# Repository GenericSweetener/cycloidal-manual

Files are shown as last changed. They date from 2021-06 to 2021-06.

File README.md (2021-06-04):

# Sections
## 1 – [Intro](https://github.com/GenericSweetener/cycloidal-manual/blob/main/README.md#11--introduction)
## 2 – [The Concepts and Components](https://github.com/GenericSweetener/cycloidal-manual/blob/main/README.md#21--the-concepts-and-components)
## 3 – [Snap Back to Reality](https://github.com/GenericSweetener/cycloidal-manual/blob/main/README.md#3--snap-back-to-reality-1)
## 4 – [Design & CAD](https://github.com/GenericSweetener/cycloidal-manual/blob/main/README.md#4--design--cad)
## 5 – [Closing and Sources](https://github.com/GenericSweetener/cycloidal-manual/blob/main/README.md#5--closing)

This guide was created for a senior capstone project at Templeton Academy based on this research question: 

What are the appropriate use cases for, benefits and drawbacks of, and best construction practices for common complex gear sets in terms of 3d printed hobbyist construction for high torque applications?

It does not answer that question (see section 5).

# 1.1 – Introduction
Cycloidal drives/reducers are extremely useful components to have at one’s disposal when working in hobbyist robotics, however a lot of the material aimed at beginners tend to be lacking in substance, missing practical application, or in some way fail to offer a complete guide through creating cycloidal drives from scratch. This is not to say that there aren’t useful materials out there, it’s just that one often has to cobble a number of them together to integrate cycloidal gearing into their project. Thus, this document was created to be a plain English single resource for understanding the theory of operation behind cycloidal drives, and understanding the methods of and best practices for their construction.

## 1.2 – The Target and Scope
Cycloidal drives have a broad range of uses in a number of fields and applications, but with that comes an extremely broad range of appropriate contents for this document. To that end, the scope of this guide has been limited somewhat by the project that sparked it, namely the joints of a low budget quadrupedal robot, called S.N.O.T (Sub-Nominal Operations Testbed) (will be linked here if files are ever published). S.N.O.T uses nema 17 stepper motors for all joints (a poor decision in retrospect) which are capable of outputting ~0.34 N⋅m of torque. The gearboxes created for this project are intended to fit into a modular system created for S.N.O.T that has space for gearboxes 60mm in diameter and ~22mm thick. The chosen target gear ratio for the cycloidal drives is 30:1, which while likely not enough to walk with, is plenty for experimenting on the test stand. The reducers are also required to be as cost reduced as possible to fit within the budget, and will be primarily 3D printed.

TLDR; We’re using nema 17 stepper motors to power 3D printed cycloidal drives of a similar footprint in robotic leg joints.

## 1.3 – Materials, Tooling, and Software
Unless otherwise stated, all modeling for this project has been done in FreeCAD, sliced for printing in Ultimaker Cura, and printed on an Creality Ender 3 using Overture PLA filament.

While all modeling was done in FreeCAD, this guide is intended to be usable with any parametric modeling software, save for the creation of the cycloidal disk (see section 4.1.1 for more). 

# 2.1 – The Concepts and Components
While this guide gets around having the user complete the majority of the complex math behind the concept of cycloidal gearing, an understanding of the theory of operation and components therein is still vital to utilizing the rest of this guide.

## 2.2 – The Basics

Cycloidal drives offer a relatively high torque density, especially compared to standard involute gearing. The way this is accomplished is visually complex, but simple enough when stripped down to the base concepts. As the name suggests, cycloidal drives rely on the concept of cycloidal, or more specifically, hypocycloidal paths. A cycloidal path is effectively the result of rolling a circle along a straight line, tracking a single point on the diameter of the circle, and plotting the position of that point as the circle rolls as a new line.  

Cycloid_f
> By Zorgit - Own work, CC BY-SA 3.0, https://commons.wikimedia.org/w/index.php?curid=4552689

Hypocycloidal paths are the same as cycloidal paths, except the circle is rolling around another circle instead of on a straight line.



While every element of a cycloidal drive is not a direct product of this concept, they all have something to do with the idea of a circle rolling around within another circle, so just keep that in mind.

## 2.3 – Getting a Grip (base understanding)


> By Petteri Aimonen - Own work, Public Domain, https://commons.wikimedia.org/w/index.php?curid=7732225

If the above animation makes sense to you immediately, good job, you get to skip most of this section. For the rest of us, this is going to take some unpacking. Rather than pick apart the actual components of a cycloidal drive, let’s start with something more conceptual. A cycloidal drive is at its core a circle, called the cycloidal disk, rolling around the inside of another slightly larger circle, called the housing (soon to be drive pins). At face value, this does not appear to be any sort of speed reducer, until one considers how it can be driven.

without shaft
> Apologies for the poor quality. Also, please note that the video loops where you see the tracked point jump.

This is where the bearing and eccentric shaft (green component of the main 3D animation) come into play. To drive the cycloidal disk’s rolling motion, there are a number of ways one could theoretically transfer power to it, but to achieve the effect of a gear reduction, there is a rather clever and simple method. First, a bearing is placed in the center of the cycloidal disk, and then the motor is attached off center to a shaft inside it. 

with shaft
> Yeah, still not sure what the yellow in the gif is. This shows 1 rotation of the input shaft / motor. Note how much the disk actually rotates.

This both means that the power source/motor is isolated in terms of rotational speed from the cycloidal disk, because the inner and outer race of the bearing can spin at different speeds, and, because the motor is off center by the same amount as the difference between the diameters of the cycloidal disk and housing, the disk is always pressed against the edge of housing. The degree to which the motor is off center is called eccentricity, and will play more of a role later. Put this all together, and when running the motor the cycloidal disk will not spin with the motor, but instead will roll along the inside of the housing, and because the circumference of the disk and housing are similar, the disk can be rolled around for one rotation of the motor but only actually spins a small amount. This is in effect a gear reduction because 1 revolution of the motor on the eccentric shaft results in less than one rotation of the cycloidal disk.

However, even if this were taking place in an ideal world where no power was lost to friction, and the cycloidal disk never slipped, there is still no mechanism by which to actually utilize the power being transferred, because the cycloidal disk is not centered and can’t have an output shaft mounted directly to it.

## 2.5 – Getting an Output (output pins and holes)
Getting power out of a cycloidal drive is less about directly connecting the cycloidal disk to an output shaft and more to do with rectifying the wobbling motion of the disk as it rotates so that the gear reduction created can actually be used. This is where the output holes and pins seen in the animation (purple) come into play. The rectifying method of choice here uses at least 3 (normally more) holes in the cycloidal disk spaced equally in a circular pattern on its face, shown below on a reference circle of a known size. 

Screenshot from 2021-06-03 16-17-28

These holes then correspond to output pins/rollers that are arranged in the same fashion and on a reference circle of the same diameter as the reference circle of the holes.



hese pins are mounted to a surface that can rotate, called the output disk (seen in purple in the animation), which is centered by a bearing of some sort in reference to the housing. What makes it possible for these output pins to mesh with the holes of the disk even though the disk is not centered while rotating is that the disk’s holes are the same as the diameter as the output pins plus the eccentricity of the disk. This in effect means that while the output pins are never centered in the output holes, their sides are able to contact the edges of the holes, rolling along the inside of the output holes and being pushed in the correct direction. This is why there need to be more than one set of pins and holes to prevent slop in the output from the pins not being directly attached to the disk, instead requiring multiple angles of contact.

## 2.6 - Getting It To Work (the cycloidal disk and drive pins)
Up until this point, a simplified model of the actual mechanism by which the gear reduction is created has been used to demonstrate the concepts around it, however this model would be extremely inefficient and borderline useless in any practical application. So, instead of relying on the friction between a smooth cycloidal disk and its housing, cycloidal drives use a set of drive  pins/rollers in the housing (silver), and a disk with corresponding lobes for those pins which is the cycloidal disk (yellow). 



> By Petteri Aimonen - Own work, Public Domain, https://commons.wikimedia.org/w/index.php?curid=7732225

The same movement is happening here as before, that wobbling roll is the same as when it was 2 simple circles, but now there’s multiple points of contact being made so the disk can’t just slip around, it can only rotate on its rolling path. The interaction between the pins and lobes is also a similar motion to the circle rolling around another circle, one could think of the disk as the pattern made by rolling one of the pins around a circle. It is also at this point that the number of pins in the housing compared to the number of lobes on the cycloidal disk come into play. Knowing that the lobes on the disk and the drive pins are in roughly the same scale to each other, similar to gear teeth, if there were the same number of pins and lobes then the disk would not be able to move because it would just be sitting locked into the pins.



That’s just going to bind up.

This is why, in this guide and in most cycloidal reducer designs, there is one more pin on the housing than there are lobes on the disk. Not only does this make room for the rolling motion to be possible in the first place, it defines the transmission ratio of the reducer in more solid terms than the difference between the circumference of 2 circles. This is to say that for every full rotation of the input shaft, the disk moves 1 (or whatever the difference between the number of pins and lobes is) pin over. With this knowledge, the gear ratio can be defined. In this example of 30 pins on the disk and 31 pins in the housing, it would take 30 rotations of the input shaft to make one full rotation of the cycloidal disk, making the transmission ratio 30:1.

## 3 – Snap Back to Reality
An understanding of the theory of operation is only so good as the practical application of those concepts. To that end, this section will translate the concepts from section 2 to what one may actually want to manufacture.

## 3.1 – Variants of the Design

This guide offers 2 main variants of the cycloidal reducer. The first is what is generally considered to be the standard design and is what is described throughout section 2, using a plate connected to the output pins as the power output for the reducer. This design will be called the driven disk design going forwards. The second variant is conceptually the same as the first, but has fixed output pins and instead rotates the housing (called the driven housing design in this guide). 

> [Standard cycloidal reducer full assembly (video)](https://youtu.be/JAcRD82Ofww)

### 3.1.2 – Driven Housing

The best way to conceptualize driven housing designs is to imagine the housing as being free floating and the cycloidal disk as limited in its range of motion to just its wobble. This is accomplished by mounting the output pins to a stationary plate, in this case the one the motor mounts to. This component is referred to here as the motor plate or lower pin plate. Now, when the housing interacts with the disk, the disk can’t rotate but the housing can, so it does.

> [Moving housing cycloidal drive in operation (video)](https://youtu.be/8ANe9f_OlMg)

Of course, the housing needs to be kept centered, won’t survive much torsion if only supported on one side, and the forces applied to it shouldn’t be transferred to the cycloidal disk. For those reasons it’s stabilized by a bearing on the top and bottom. The bottom bearing connects to the motor plate, and the top bearing connects to a plate that has screws running down through the drive pins to connect to the motor plate.

> [Drivin Housing cycloidal reducer full assembly (video)](https://youtu.be/nldJB2Xw-ws)

### 3.1.3 – A Note on Stacked Disks

While not utilized in this guide, it is common practice to reduce the vibration caused by the off center rotation of the cycloidal disk by having 2 disks in the same housing 180 degrees offset from each other. 

Screenshot from 2021-06-03 16-28-52

These disks will rotate in the same direction and at the same speed so their output holes still line up with each other (provided they are symmetrical across both the x and y axis). This means that while rotation is still taking place, the shifting weight of one disk is always offset by the other. To accomplish this the eccentric shaft is split into 2 cams so the top and bottom disks are driven 180 degrees offset from each other.

Screenshot from 2021-06-04 09-00-27

## 3.2 – Bearings – An Epic Saga
Anyone genuinely considering manufacturing a cycloidal drive by means of 3D printing will have likely noticed the very high number of surfaces that need to be in contact with each other in even the most basic of cycloidal designs. The good news is that all but the edge face of the cycloidal disk can be replaced by a friction reducing element, however this may not always be the best design decision. At any rate, a cycloidal drive that will carry any sort of load requires at the very least 2 bearings: 1 in the center of the cycloidal disk and another to keep the output ring centered. 

### 3.2.1 – The Required Bearings – Cycloidal Disk
The bearing in the center of the cycloidal disk (drive bearing) both relies on and can limit some of the primary dimensions of the cycloidal drive, so care should be taken when finding a bearing to use. Firstly, keep in mind that this bearing is what makes it possible to use an eccentric shaft, so some thought needs to be given to the inner dimension of the bearing so that the the desired level of eccentricity is both possible and won’t create a situation where the hole in the eccentric shaft that accepts the input shaft of the motor is extremely thin on one side. (learned that the hard way).

Screenshot from 2021-06-04 09-03-49

A good rule of thumb is that (assuming the eccentric shaft is accepting a metal output D-shaft from the motor) the inner diameter of the bearing should be equal to the diameter of the motor output shaft plus the disk’s eccentricity plus however thick you want the thinnest part of the eccentric shaft to be (at least 3mm).

Another point to consider is that the cycloidal disk should be a similar thickness to the drive bearing. This ensures that the bearing will be able to transfer power to the entire edge of the cycloidal disk. It’s also a good idea to have a ridge of some sort modeled in the hole for the bearing so it can be pressure fit until bottoming out.

Screenshot from 2021-06-04 09-05-26

One final element of note is that, especially with a 3D printed disk, the bearing is likely to be the heaviest spinning component, and will be spinning off center to the rest of the assembly. This can be dealt with by using a stacked design (see 3.1.1), but suffice it to say that a lighter bearing will create less vibration.

### 3.2.2 – The Required Bearings – Output Pins / Output Ring (output bearings)
To center the output disk/pins to the housing, it is advised that a relatively large bearing is used with an inner diameter that is able to fit around the outside of the output disk, and is therefore larger than the outer edge of the output pins. This then mounts into the housing.



This method allows the forces applied to the output ring to be braced against the housing, which can be reinforced depending on the load required. While this method is strong and robust, it does have some drawbacks. Cost is by far the largest issue bearings of this specification can add to a project, with the example bearings (inner diameter = 45mm, outer diameter = 85mm, thickness = 7mm) costing roughly $10 per bearing, which can get quite expensive for something like a quadrupedal robot, especially when using cycloidal designs that require 2 output bearings (3.1.2). These larger bearings are also quite heavy, the aforementioned bearings in particular weigh ~50g.

### 3.2.3 – Output Pins

Using something other than 3D printed plastic for output pins is by far the most valuable upgrade one can make to their budget cycloidal drive, because it increases the strength of the assembly by a massive degree without adding too many more individual components. The drawbacks of 3D printed output pins is quite obvious when one considers the relatively low force required to shear off the pins on the layer lines. 

Screenshot from 2021-06-04 09-15-10

> Video of pin failure [here.](https://youtu.be/O2v3M0Q1Ow4)

The 2 routes one can take in making reinforced output pins are using small bearings or using round nylon standoff spacers in place of 3D printed output pins. The only real difference from a modeling and construction perspective is that rather than modeling pins to be printed on the output disk, one would have holes through it, potentially with hexagonal holes on the other side going partially through it to capture a nut. And of course a bolt/screw and a nut is necessary to keep the bearing / nylon spacer in place (as seen in 3.2.2).

This guide uses 7mm outer diameter 3mm inner diameter nylon spacers as output pins.

### 3.2.4 - Drive Pins
Using bearings in place of 3D printed drive pins can significantly reduce wear and friction within a cycloidal drive, however these benefits come with increased weight, drive pin diameter, cost, and complexity. To that end this guide did not include testing with bearings in place of drive pins and does not have modeling instructions for them. 

### 3.2.5 – A Note on Pressure Fitting Bearings
This guide requires a fair number of bearings to be pressure fit into 3D printed housings, so some thought and testing of bearing fitment should be done before printing components. It is therefore advised that you create test pieces for bearings to fit into / to fit into bearings and undergo some trial and error to find dimensions that can tightly hold or fit into a bearing without being deformed by it or requiring forceful persuasion (Take it from someone who’s broken a bearing with a hammer). When making test pieces, be sure to use the same print settings as on the final components. Time spent in this process will save on test prints later down the line.

## 3.3 – Choosing an Output Pin Circle
The output pin circle is the reference circle that passes through the center of the output holes on the cycloidal disk and through the center of the drive pins as mentioned in section 2.5. Especially on the smaller cycloidal disks used in this guide, it is of the upmost importance to ensure that the output holes on the cycloidal disk have enough material surrounding them as to not create thin weak spots in the disk for deformation or cracking to occur. A good rule of thumb is to have the output pin circle roughly centered on the disk, and try to have ~3mm of material around the holes.

Screenshot from 2021-06-04 09-17-33

However, this is not always possible because the inner diameter of the drive bearing can limit the maximum size of the output pin circle, and should also be taken into account. This is why the output holes on the reference models provided are not perfectly centered on the cycloidal disk.



# 4 – Design & CAD
Now for the long boring part. This section is a step-by-step guide for designing the various components of driven housing and driven disk cycloidal reducers. The reference models created for this project are provided here in .FCStd format, editable and exportable in FreeCAD.

## 4.1 – Cycloidal Disk
This guide uses the process of modeling the cycloidal disk as the focal point for setting all major parameters of the cycloidal drive.

### 4.1.1 – Why FreeCAD?
The two common ways to model a cycloidal disk are mathematically defining it from scratch as a curve, or using a disk generation tool that creates a disk based on easily inputted parameters. This guide is aimed at beginners to cycloidal gearing, and so it was decided that a disk generation tool should be used to lower the overall difficulty for the end user. Because FreeCAD was used for all modeling in this project, the [FCGear workbench](https://wiki.freecadweb.org/FCGear_Workbench) was used to generate the disk. However, because this guide is intended to be usable agnostic of the chosen modeling software, this section has been split into a video which walks a user through the complete process, from installing FreeCAD to exporting the disk for printing; and a written section intended for those already familiar with FreeCAD.

If, however, you would prefer to mathematically define the disk in the program of your choice, [this paper](https://blogs.solidworks.com/teacher/wp-content/uploads/sites/3/Building-a-Cycloidal-Drive-with-SOLIDWORKS.pdf) has been provided to aid in that process. 

### 4.1.2 – Modeling for Complete FreeCAD Beginners

> [Video](https://youtu.be/ldznm4VQLB4)

### 4.1.3 – Modeling for FreeCAD Users
As mentioned in the introduction, this section will be making use of a cycloidal disk generated using the FCGear workbench, so start by installing it through the Addon Manager (in the Tools tab) or through the manual instructions found on the [wiki page](https://wiki.freecadweb.org/FCGear_Workbench). It should be noted that while cycloidal disk generation is a feature of the FCGear workbench, it is not documented on its wiki.freecadweb.org page.

### 4.1.4 – Generating the Disk

* Create a new file and add a new Part Design body. This guide will be using the Part Design workbench for all modeling except for the generation of the disk.
* Within the body, use the “Gear” workbench to create a new hypocyloid gear 
* Notice that it generated 2 separate disks and a set of pins, however these pins and extra disk will be disabled shortly
* Selecting the hypocycloid gear in the combo view will allow for the adjustment of all perimeters, the details of which are listed below:

        ◦ Base
            ▪ Label
                • The label of the model within FreeCAD.
        ◦ Disks
            ▪ disk_height
                • The thickness of the individual disks generated
                    ◦ This should be set to the thickness of the center bearing
            ▪ show_disk0
                • Shows or hides the top disk
                    ◦ FCGear generates a set of 2 disks in the offset configuration as detailed in section 3.1.1, however obviously for the sake of 3d printing the individual disks this is not ideal. This guide advises setting show_disk1 to false and only working with disk0.
            ▪ show_disk1
                • Shows or hides the bottom disk
        ◦ Pins (mostly irreverent to this guide)
            ▪ center_pins 
                • This setting determines if the pins generated by FCGear will be vertically centered in reference to the disks generated. 
                    ◦ Note: This is only applicable when one of the disks is set to not be shown, as it will center the pins regardless of this setting if both disks are shown.
            ▪ pin_height
                • The height of the pins.
            ▪ show_pins
                • Determines if the pins will be shown or not.
                    ◦ This guide does not use the pins generated by FCGear, so this should be set to false.
        ◦ gear_parameter
            ▪ eccentricity
                • This sets how far off center the rotation of the disk will be.
                    ◦ Finding the right eccentricity is a balance between what can be produced using your drive bearing (see 3.2.1 for more) and what is possible given the constraints of how tightly packed the drive pins are.
                    ◦ Eccentricity also refers to how aggressive the lobes of the disk are, basically how far into the disk the drive pins go.
                        ▪ Because of this, it’s best to have a relatively high eccentricity to increase the lifespan of the drive, because less aggressive lobes will round over more easily.
                            • Eccentricity cannot be set infinitely large, though. To this end is advised that eccentricity is the last value set if all other values are known, so that trial and error can be used to get the highest eccentricity disk that is still solvable.
            ▪ hole_radius
                • The radius of the center hole that will accept the drive bearing. See 3.2.5 for pressure fitting this bearing properly.
            ▪ pin_circle_radius
                • This sets the radius of the reference circle that passes through the center of each drive pin.
                    ◦ This roughly corresponds to the radius of the housing, but to exactly equate the two see section 4.2.1
            ▪ pressure_angle_lim
                • The naming of this value suggests that it would limit the possible pressure angles between the pins and disk, but it only seems to inform how pressure_angle_offset effects the disk. Without FCGear’s wiki defining these values, it is difficult to say the exact nature of these settings, however leaving them at their default settings has given no issues in testing.
            ▪ pressure_angle_offset
                • See previous value (leave at default)
            ▪ roller_diameter
                • The diameter of the drive pins
                    ◦ Ideally this should be over 2mm
            ▪ segment_count
                • This determines the number of b-spline segments used to define the disk. In testing, using the same number of segments as teeth_number / lobes most frequently produced valid results.
                • It should also be noted that computation time for actions on the disk will increase   with more sections added.
            ▪ teeth_number
                • The number of lobes on the disk
                    ◦ Remember that there will be 1 more drive pin than lobes on the disk
                    ◦ The transmission ratio of the reducer will be teeth_number:1
        ◦ version
            ▪ version
                • Indicates the version of FCGear used to generate the gear
                    ◦ It cannot be changed

### 4.1.5 – Output Holes
The disk generated will be offset on the x axis by the eccentricity, which makes automatically spacing the output holes on a reference circle centered to the center of the disk rather than the origin of the model difficult, and can make creating the holes correctly after exporting to another program a pain. Ideally the disk would be moved to be centered in reference to the origin of the model, but I had difficulty making that work in the part design workbench. Those more familiar with FreeCAD may have a better solution to what is about to be shown, but this does work.

First, create a sketch mapped to the top face of the disk, and use the link to external geometry tool on the center circle. 



You can see the discrepancy between the center of the disk and the origin of the model here. Next toggle on construction mode  and use the “create a regular polygon” tool to first select a shape with the same number of points as you require output holes, and then create it centered to the newly linked external geometry. To fully constrain the sketch be sure to do something to fix the rotation of the regular polygon. In this case, a square is used to create 4 holes.



Toggle out of construction mode and place a circle on each point, set them equal to each other, and then set their diameter. In this case, 7mm diameter nylon pins are to be used for the output pins and the disk has a 0.8mm eccentricity. However, the printer and filament used for testing has a habit of shrinking the final model slightly, so 0.1mm was added to the theoretical diameter (7.8) of the output holes.

Set the diameter of the reference circle. For more information on determining the best pin and reference circle dimensions, see 3.3.



Finally, use this sketch to cut a pocket through the disk.



## 4.2 – Housing
The primary function of a cycloidal drive’s housing is to support the drive pins and accept bearings for the output disk(s), and to that end, while being one of the more complex elements from a modeling perspective, is still a relatively simple component to create.

### 4.2.1 – The Main Body
When modeling the housing, it’s best to start with the section that will contain the drive pins and work outwards from there. The goal of this section is to mold the drive pins into the housing for extra support rather than have them free standing.



The most important value to consider here is the inner diameter of the hollow cylinder that makes up this section. The pins contact with the housing should be maximized, but not the the point of  interfering with the cycloidal disk’s travel. 



To accomplish this, first take the pin circle diameter (remember to convert from the radius) as determined in (SECTION), and then subtract the pin diameter from it. In this example that would be 56 – 2.7 = 53.3. This gives a circle around the inner edge of the pins:



Because the eccentricity of the disk is just effectively how far it extends towards the pins and how deep the troughs are, adding 4 times the eccentricity to this value will give the maximum diameter of the area the disk will travel in, and thus the minimum size for the inner diameter of this part of the housing. In this case, 53.3 + 4(0.8) = 56.5. Multiplying the eccentricity by 4 may seem counterintuitive at first, but remember that it refers to the height of the peaks and depths of the troughs in terms of a center line in the middle of them, hence multiplying it by 2, and it is also in terms of the radius, so when working with diameters one has to multiply it by 2 again.

This plus preferably an extra 0.5mm at least (preferably more, but when working at this scale there simply isn’t much space to be spared) for extra clearance to accommodate for the disk being slightly too large or the housing flexing gives the inner diameter for the pin section of the housing.

The outer diameter  of this section will determine the external diameter of the rest of the gearbox, and may need to change later depending on if the bearing for the output disk requires more space to be mounted. This value should be no less than 3mm to prevent significant flexing of the housing.



This section is then extruded to the thickness of the disk that will be within it plus a millimeter or so of extra clearance to prevent it from rubbing on the top and bottom of the gearbox. In this case, the housing will be extruded by 8mm.



## 4.2.2 – Drive Pins

The number of pins, their diameter, and their reference circle diameter were all determined in section (SECTION), so now all there is to do is model them appropriately. In this case, 31 pins (remember that the number of pins is one more than the number of lobes on the disk) with diameters of 2.7mm, on a reference circle with a radius of 28mm. Rather than model each pin in one sketch, a single pin will be modeled, extruded, and copied in a polar pattern. While not necessary, to have the pin line up visually with the default position of the disk generated in section 4.1, align this first pin on the x axis to the left of the y axis as seen in the model below.



The pin is then padded to the same thickness as the ring, in this case 8mm, and then copied in a polar pattern, in this case 31 times.



### 4.2.3 – Bearing Mounts

For both moving housing designs and output disk designs, there is a requirement for a large bearing at the top of the housing to center the output disk. The only difference between the two designs’ housings is that moving housing gearboxes will have another bearing on the bottom of the housing, and output disk variants will have a bearing at the top and a motor mount on the bottom. 

This is where cooperation between bearing choice and housing size come into play, because the ideal outer diameter for the output bearing is slightly larger than the inner diameter of the housing.  IT should be such that the hole it press fits into does not hang over the rest of the housing, which both means that during construction the disk can be inserted and during printing support material is not required. The outer diameter of the bearing should also not be too large as to require the housing’s total diameter to be increased to accommodate for it. To that end, a bearing with an outer diameter of 58mm was used. This was as close to perfect as the size constraints and bearing availability would allow.



The modeling of this is extremely simple, only requiring a sketch on the top face of the housing with a central hole capable of fitting the bearing, in this case 58.15mm, and an external diameter set equal to the other housing section. If the bearing section’s wall is too thin (preferably 3mm), increase the overall diameter.



This is then extruded to the thickness of the bearing that will mount within it.

### 4.2.4 Moving Housing Designs

For designs with a moving housing, simply repeat section 4.2.3 on the bottom side of the housing, as this will be used to mount a bearing on both sides of the gearbox.



How power is derived from this ring is up to the user, however for the example application a hole for REV Robotics 15mm x channel has been modeled.



### 4.2.5 Stationary Housing Designs
If a stationary housing is to be used, a motor mount needs to be created on the bottom of the housing. 



To create a motor mount, create a sketch on the bottom face of the housing with an outer diameter matching that of the housing, and holes for the motor screws and a space for the drive shaft to enter the housing.



For the example nema 17 motor, a centered square pattern of 4 m3 screws spaced 31mm from each other. The center hole must be at least the outer diameter of the eccentric shaft, however if a bearing is desired to brace the input shaft, be sure to include spacing for the bearing.

The screw holes will need to be countersunk to avoid the cycloidal disk fouling on them. So, when extruding the motor mount plate, take into account both the space taken by countersinking the screws and having enough material for them to mount to. In this case, the screw heads are 2mm tall and ~6mm in diameter, so the bottom plate will be extruded 5mm to allow for 2mm of countersinking and 3mm of material underneath them.



Finally a chamfer (1mm) should be applied to the screw countersink holes to minimize friction between their edge and the disk.



## 4.3 – Output Ring & Pins
Output disks and pins are perhaps the simplest component to model but bear the majority of the forces imparted onto the cycloidal drive.

### 4.3.1 – Driven Disk – 3D Printed Pins
This is the simplest version of the output disk, and integrates the output pins and output disk into one printed component. It is not advised for high load bearing applications (see 3.2.3).

First, the output disk is created, which is simply a cylinder intended to fill the interior dimensions of the output bearing. In this case a 45.25 mm disk extruded to 7mm thick.





Next, on one face of the disk, model a pin whose center is on the reference circle found in section 2.3.



Next extrude that to the thickness of the cycloidal disk, and use a polar pattern to duplicate it evenly around the disk for however many pins are required.



Mount whatever load is to be driven to the other side of this plate. Also, be sure to account for the motor drive shaft extending too far into the housing and fouling on the output disk. You may need to place a hole in its center to account for this.

### 4.3.2 – Driven Disk With Nylon Pins / Top Plate of Driven Housing Variants
This is effectively the same as the 3D printed pin version, except instead of pins being mirrored with the polar pattern, holes for screws/bolts, in this case 3mm screws, are used. This plate can either be used as the driven output plate or as the top plate of driven housing designs.



For driven output disk designs, if a flush face on the outside face of the is desired, add hexagonal holes to capture nuts on the other side of the disk. 



This is not required for using this model in driven  housing designs as the screw heads will be on this plate, not the nuts. However countersinking can be done for anesthetics or to use a shorter screw.

For driven disk designs, it’s then just a matter of screwing on nylon spacers.

### 4.3.3 – Moving Housing Motor Plate
Ideally, the motor plate of a moving housing cycloidal drive would be identical to the top plate, save for space to capture nuts for the screws running through the pins, having holes to mount the motor, and a hole for the motor drive shaft, but because in this case the motor mounting holes could not fit within the inner diameter of the output bearing, a slightly larger adapter plate was created.

Example:



The same starting plate is taken to fill the inner diameter of the output bearing, but now a larger (55mm diameter and 5mm thick to allow the screw heads to have 2mm countersinking) plate is added to its bottom face to accommodate the motor mounting screw locations.



Motor mounting holes are then cut from the bottom face through the model.



These then have 7mm diameter holes cut from the top to give clearance for the screw heads.



In this case, the pockets are 9mm, 7mm to clear the bearing mount section and another 2mm for countersinking of the screws.

Next, the same holes for mounting output pins are added, with corresponding hexagonal pockets on the other side to capture a nut.



Finally, a centered hole, in this case 15mm in diameter is added to accommodate for the eccentric shaft passing into the housing.



## 4.4 – The Eccentric Shaft
The design of the eccentric shaft is heavily dependent on the motor drive shaft that it interacts with, however the base concept of the shaft being offset from the input shaft is constant. In this case, a D shaft coming from a nema 17 motor is the input shaft, and a very simple eccentric shaft was created to cover the entire 18mm section of the motor output shaft with a flat side machined onto it. 

First, a hole tested to snugly accept the D shaft was modeled.



Then a circle that has been test fit with the inner diameter of the drive bearing (in this case 7.89mm) is placed offset by the  eccentricity from the input shaft.



Note that the flat side of the D shaft, where most power will be transferred, is placed in the thicker area of the shaft. This is a poorly chosen bearing inner diameter because of the extremely thin section it creates. See 3.2.1 for best drive bearing practices.

This is then extruded by 18mm.



# 5 – Closing

The exact intent for this project has been a moving target from it’s conception to completion, and this is well reflected in the initial research question. This project was originally intended to be a research paper comparing different gearbox designs, however time constraints and what was viewed at the time as an apparent need for something like what this final product has become, have shaped it into something different entirely. This guide takes the primary focus of the research question, namely understanding at least one complex gear set that can be manufactured via 3D printing, and expands on it in a way that is more targeted to what may actually be useful to its intended audience.

Hopefully this guide was at least of some use someone, slapdash as it may be in places.

## 5.1 – Sources

Thube, Sandeep, and Bobak, Todd. *Dynamic Analysis of a Cycloidal Gearbox Using Finite Element Method*, American Gear Manufacturers Association, 2012, http://edge.rit.edu/content/P15201/public/MSD%20II/Research%20Papers%20Humanoids/Unknown%20-%20AGMA%20Technical%20Paper%20Dynamic%20Analysis%20of%20a%20Cycloidal%20G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,%20Bobak.pdf

Younis, Omar. *Building a Cycloidal Drive with SOLIDWORKS*, The SOLIDWORKS Blog, https://blogs.solidworks.com/teacher/wp-content/uploads/sites/3/Building-a-Cycloidal-Drive-with-SOLIDWORKS.pdf

Bruton, James. *Experiments with Cycloidal Drives*. YouTube, 2021, https://www.youtube.com/watch?v=pWMB5VbLb6w&t

Bruton, James. *3D printed Cycloidal Drive V2*. YouTube, 2021, https://www.youtube.com/watch?v=pWMB5VbLb6w&t

Muthe, Abhijit. et al. *Design and Fabrication of Cycloidal Gearbox*. International Research Journal of Engineering and Technology, 2018, https://www.irjet.net/archives/V5/i4/IRJET-V5I4565.pdf

TL

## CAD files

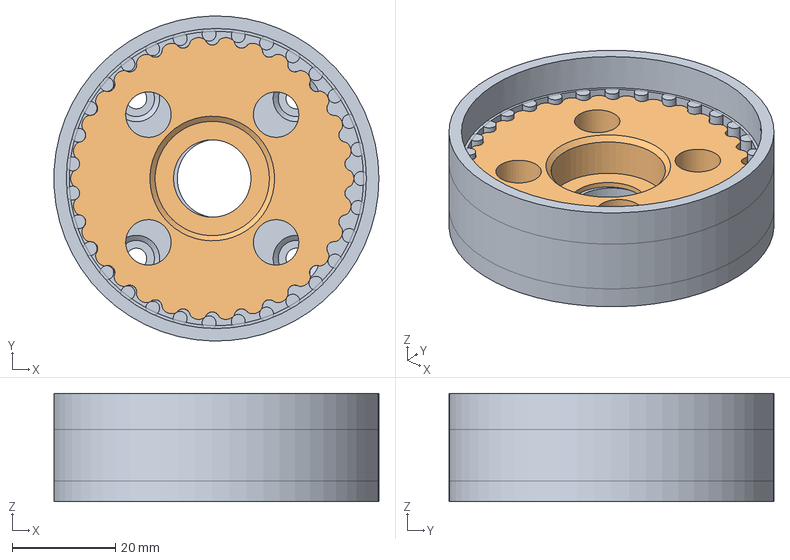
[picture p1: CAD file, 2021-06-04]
Driven disk/Disk and Housing.FCStd
63.0 x 63.0 x 21.0 mm

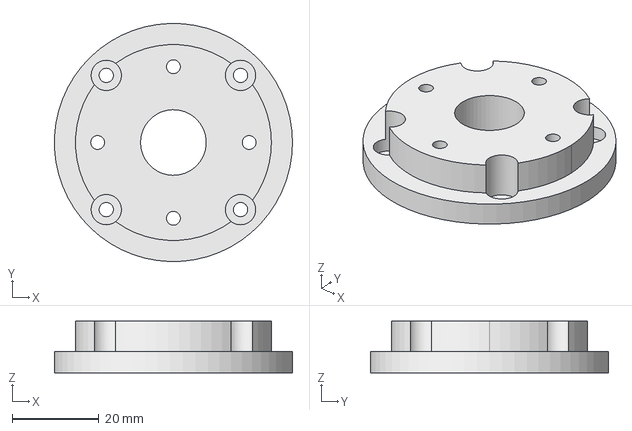
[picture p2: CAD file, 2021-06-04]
Driven Housing/Motor Ring.FCStd
55.0 x 55.0 x 12.0 mm

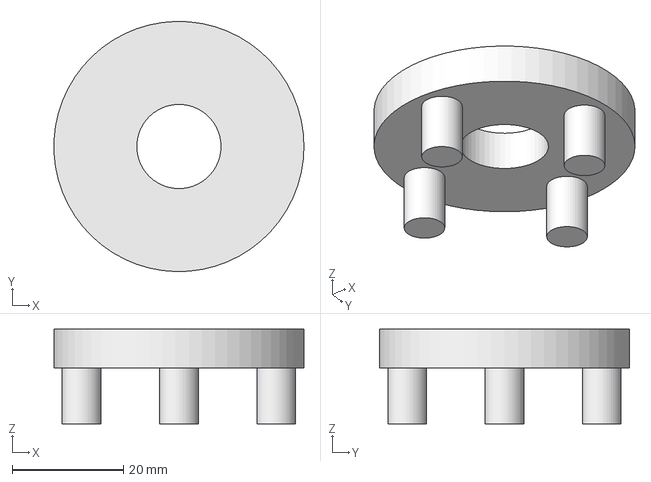
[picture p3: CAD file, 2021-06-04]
Driven disk/Output ring with pins.FCStd
45.0 x 45.0 x 17.0 mm

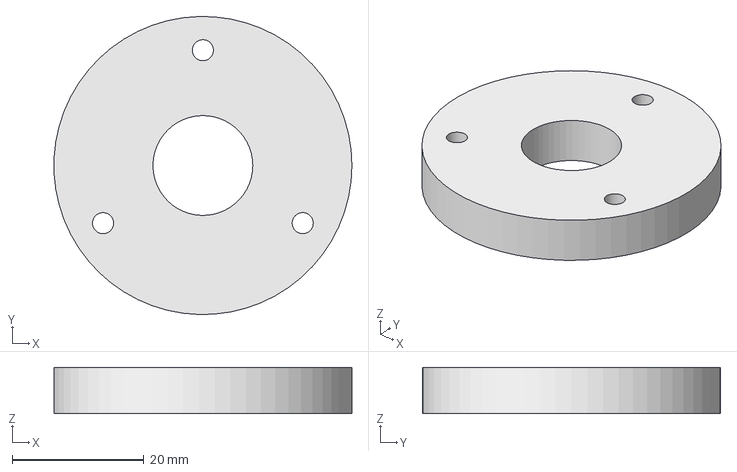
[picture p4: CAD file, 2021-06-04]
Driven Housing/Output ring without pins.FCStd
45.2 x 45.2 x 7.00 mm

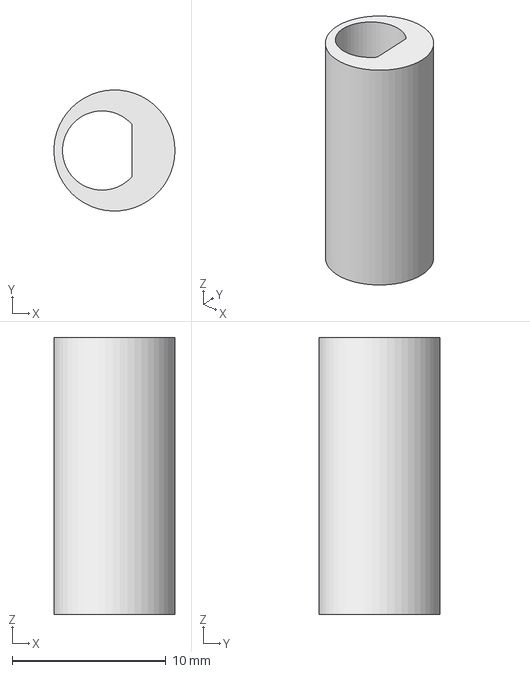
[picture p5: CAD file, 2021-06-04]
Driven disk/Shaft.FCStd
7.86 x 7.87 x 18.0 mm

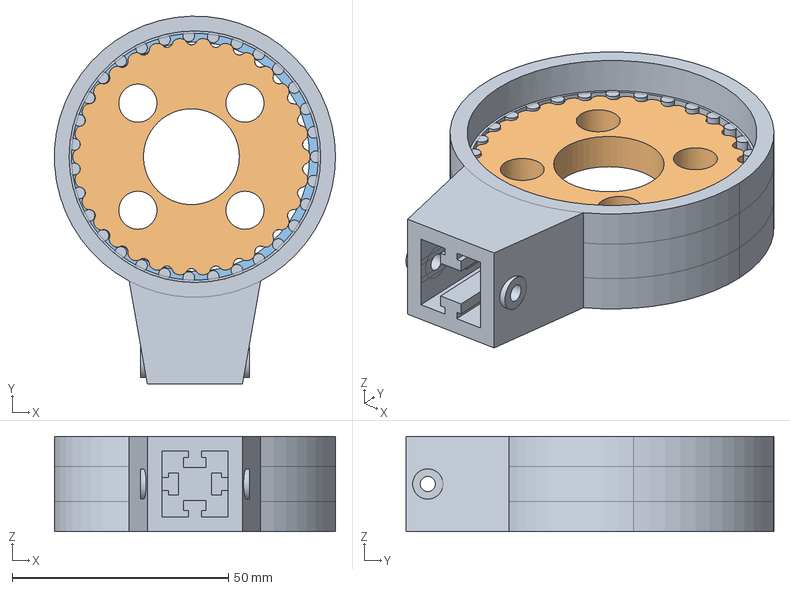
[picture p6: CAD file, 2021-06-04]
Driven Housing/Housing and disk - with mount.FCStd
64.9 x 85.0 x 22.0 mm
Support material

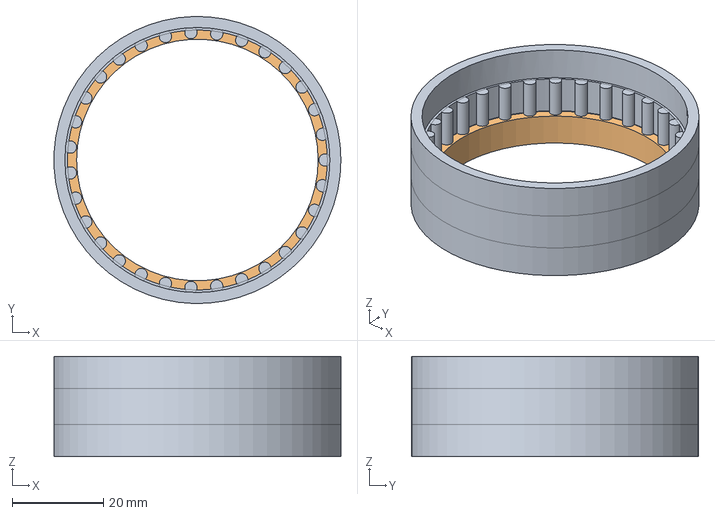
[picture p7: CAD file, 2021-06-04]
Driven Housing/Housing and disk.FCStd
63.0 x 63.0 x 22.0 mm
Support material
